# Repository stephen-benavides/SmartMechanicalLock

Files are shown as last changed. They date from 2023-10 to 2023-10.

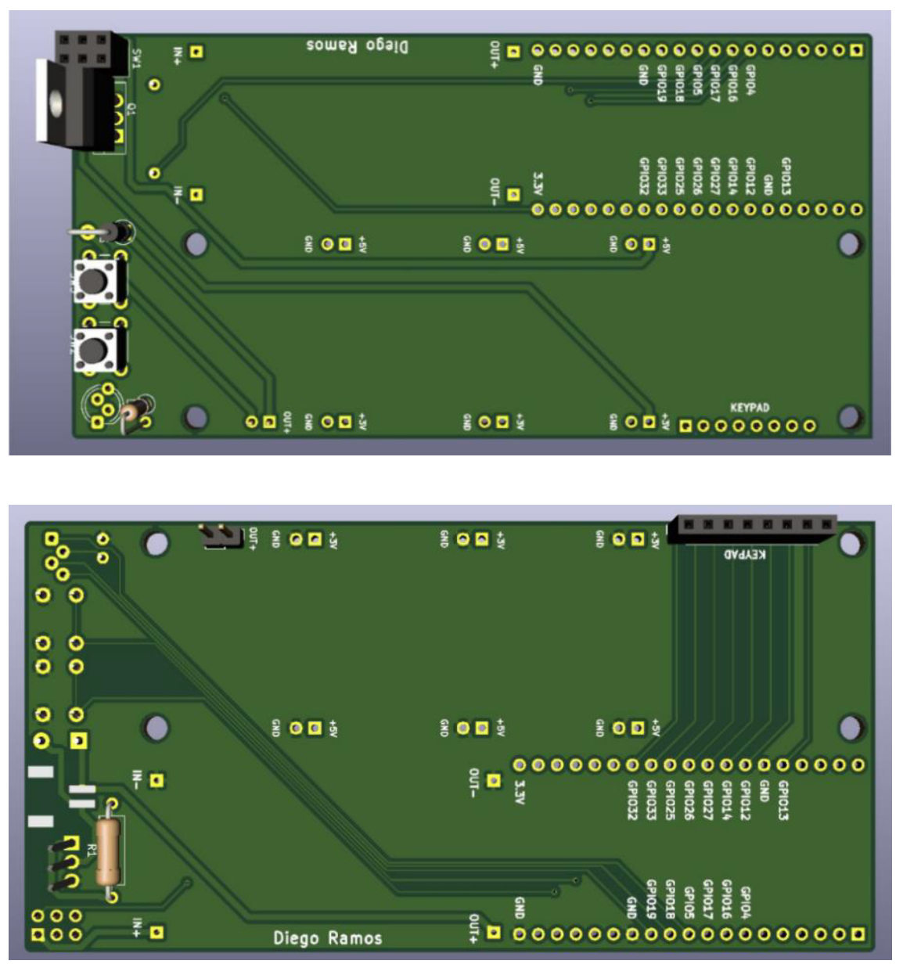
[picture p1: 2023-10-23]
Senior Project - Beta/Smart Lock (Pending Name)-20201122T195937Z-001/Smart Lock (Pending Name)/Schematics/Screen Shot 2019-09-06 at 3.24.47 PM.png

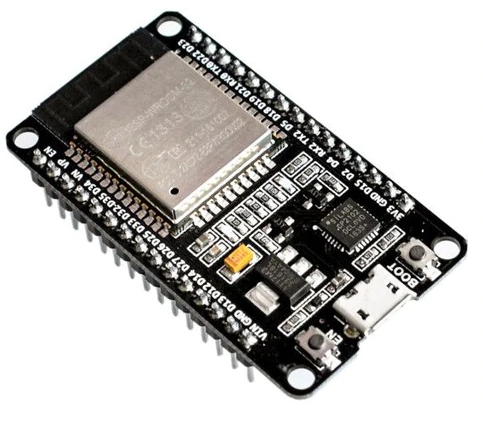
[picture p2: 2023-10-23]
Senior Project - Omega/ESP32/2019-02-23 (1).png

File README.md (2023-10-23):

# SmartMechanicalLock
Project contains all elements from the design of the PCB for the mechanical locks and its components as well as the mobile application to access the app to send the necessary commands to lock/unlock the lock and to store all sensible information within the cache of the android device

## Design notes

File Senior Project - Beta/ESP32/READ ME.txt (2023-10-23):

https://discordbots.org/servers/514901094950895651
wickr me 
null byte (Youtube)

arduino extension on visual studio code 
caprtea vacia, la abres con arduino uno . 

F1>Arduino initialize 

F1> carpeta en blanco (F1 hace todos los comandos)

F1> arduino examples
  > arduino config  
  > arduino serial monitor

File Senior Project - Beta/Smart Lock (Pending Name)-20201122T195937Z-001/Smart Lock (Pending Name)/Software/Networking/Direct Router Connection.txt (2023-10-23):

#include <WiFi.h>

void setup()
{
Serial.begin(9600);

  WiFi.disconnect();
  delay(3000);
  Serial.println("Initializing");
  WiFi.begin("wifi4beer","password");
  while ((!(WiFi.status() == WL_CONNECTED))){
    Serial.print("...");
    delay(300);

  }
  Serial.println("Connection Successful");
  Serial.println("Local IP address:");
  Serial.println((WiFi.localIP()));

}

void loop()
{

}

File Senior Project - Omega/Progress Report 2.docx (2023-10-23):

Project Work Progress Report No ______

Date:______________ Team #:_________

Project Title: _________________________________________________________

Submitted by: ___________________________________________________________

1. Project progress since last report:

Our goal this week is to be able to connect the ESP32 to a LAN network and stablish a control point for all the incoming connection using a cellphone as the router.

We were able to find the ESP32-WROOM-32D MCU IP address within the Arduino IDE serial monitor, now we are trying to send a pin signal to the computer wirelessly from the ESP32-WROOM-32D MCU.

2. Milestones achieved:
- Wireless connection stablished between the ESP32-WROOM-32D MCU and the computer by Stephen Benavides 02/20/2019
3. Problems and roadblocks, if any:
4. Is project on schedule? YES__X___ NO____
5. Next steps: (elaborate specifically on any problems listed in 3 and if the answer in 4. Is NO)

(You may use more pages, if needed)

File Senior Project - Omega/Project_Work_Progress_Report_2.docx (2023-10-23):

Project Work Progress Report No 2

Date: 02/23/2019 Team #: 33

Project Title: Anti-theft Package Security Home System (APSHS)

Submitted by Gregory Escobar, Stephen Benavides, Shawn Carnevale, Geomar Reyes

1. Project progress since last report:

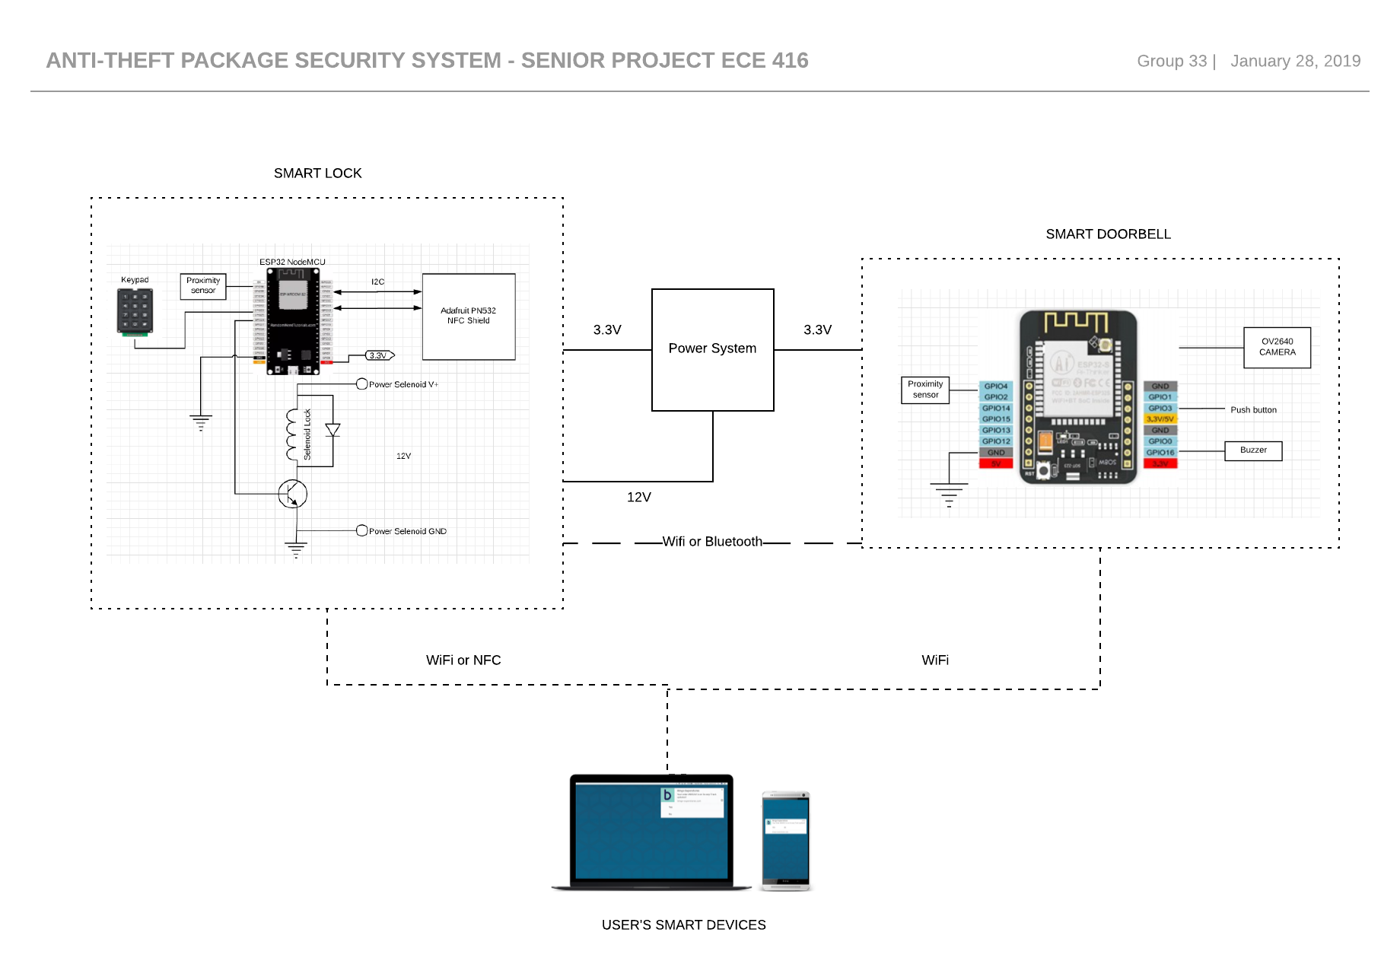
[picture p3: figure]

This is an updated version of the schematic for the whole project

Figure 1 Anti-theft package Security System

Communication between ESP32S and Adafruit PN532

Our team is still working to stablish communication between the ESP32-WROOM-32 and the PN532 using I2C communication protocol.

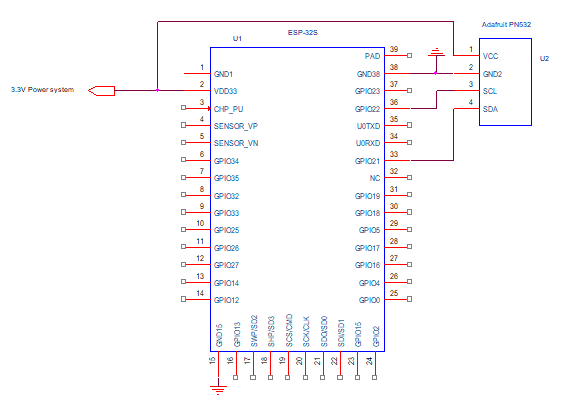
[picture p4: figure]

Figure 2 ESP32S and PN532 i2C wiring guide

Power System

For the power system our team have just picked out and received some new equipment. The focus this week was to find a way to charge and discharge the battery to and to keep a steady voltage because most of our components operate between 3.3-5 volts. The main issue was to design something that was simple and to keep it as affordable as possible. We found the solution of how to do that with a single component which was affordable and met our needs and specifications. Next week the goal will be to do more schematic work to finalize the design so we can move forward to start to build our power system onto a breadboard.

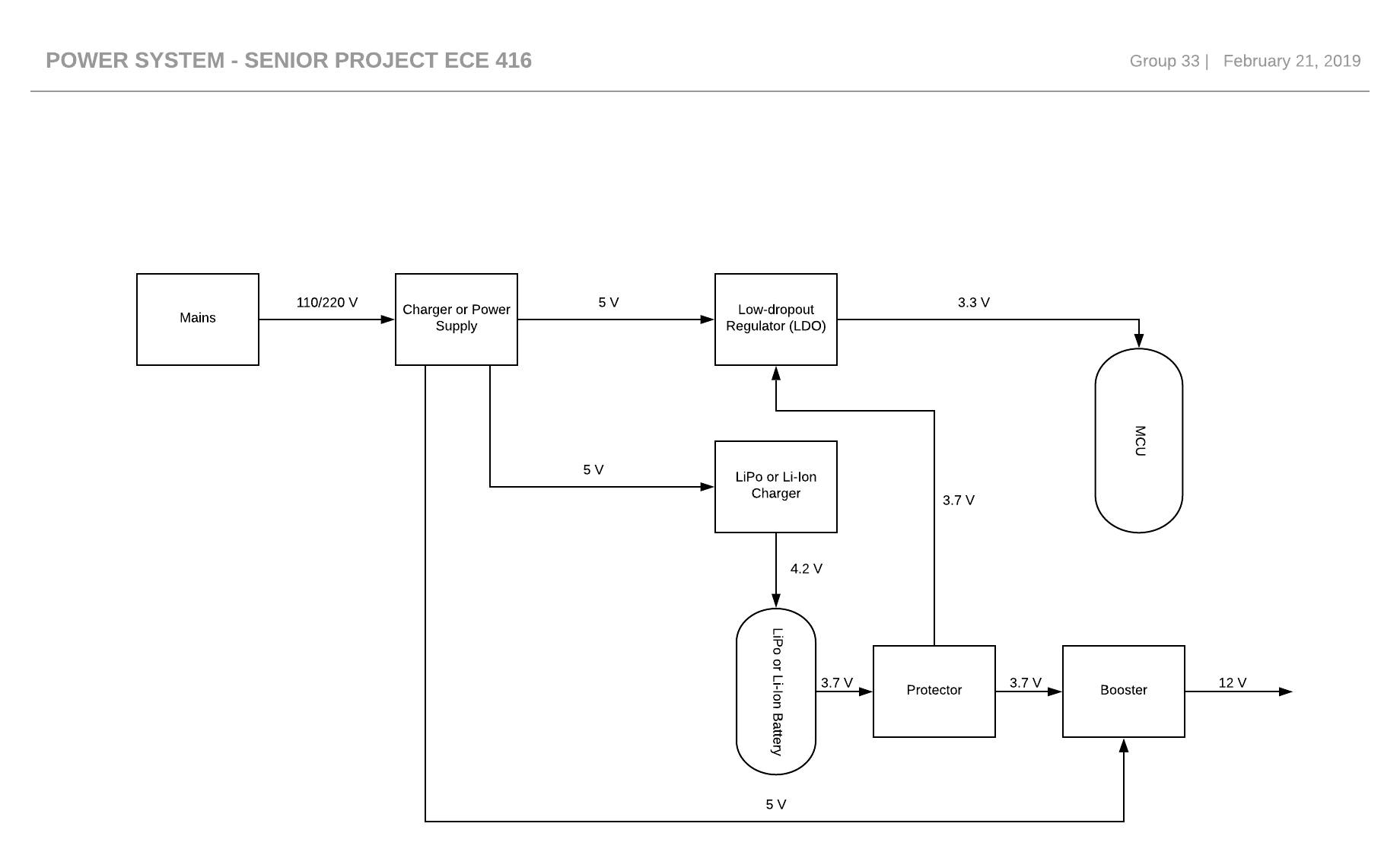
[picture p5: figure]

Figure 3 Power System

2. Milestones achieved:

Power System design was finalized by Shawn Carnevale and Gregory Escobar 02/21/19

3. Problems and roadblocks, if any:
4. Is project on schedule? YES__X___ NO____
5. Next steps: (elaborate specifically on any problems listed in 3 and if the answer in 4. Is NO) (You may use more pages, if needed)

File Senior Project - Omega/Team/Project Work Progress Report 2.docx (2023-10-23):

Project Work Progress Report No 2

Date: 02/23/2019 Team #: 33

Project Title: Anti-theft Package Security Home System (APSHS)

Submitted by Gregory Escobar, Stephen Benavides, Shawn Carnevale, Geomar Reyes

1. Project progress since last report:

Gregory Escobar and Shawn Carnevlale:

This is an updated version of the schematic for the whole project

Communication between ESP32S and Adafruit PN532

Our team is still working to stablish communication between the ESP32-WROOM-32 and the PN532 using I2C communication protocol.


Figure 1 Anti-theft package Security System


Figure 2 ESP32S and PN532 i2C wiring guide

Power System

For the power system our team have just picked out and received some new equipment. The focus this week was to find a way to charge and discharge the battery to and to keep a steady voltage because most of our components operate between 3.3-5 volts. The main issue was to design something that was simple and to keep it as affordable as possible. We found the solution of how to do that with a single component which was affordable and met our needs and specifications. Next week the goal will be to do more schematic work to finalize the design so we can move forward to start to build our power system onto a breadboard.


Figure 3 Power System

Stephen Benavides:

Our goal this week is to be able to connect the ESP32 to a LAN network and establish a control point for all the incoming connection using a cellphone as the router.

We were able to find the ESP32-WROOM-32D MCU IP address within the Arduino IDE serial monitor, now we are trying to send a pin signal to the computer wirelessly from the ESP32-WROOM-32D MCU.

I wanted to add Wireshark to our operations, but it might not be necessary yet. It is used for troubleshooting and diagnostic of the networks, this will be useful when trying the use the UART protocols to connect online using the web app to see if there are any problem with the connection.

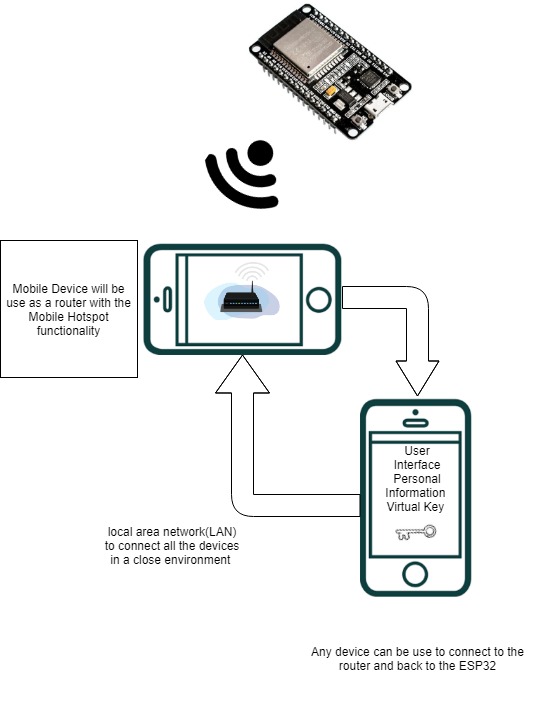
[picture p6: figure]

Figure 4. ESP32 connected to network

Geomar A. Reyes

Our goal for this week is to make the login page of the android app functional so that we can start to put name of customer and their ID in to a data base that will be connected to the app. This app will ask for a person username which will be provided by an administrator and the password will be made by the customer. The login screen will be able to match the username and password input by the customer with the one in the database.

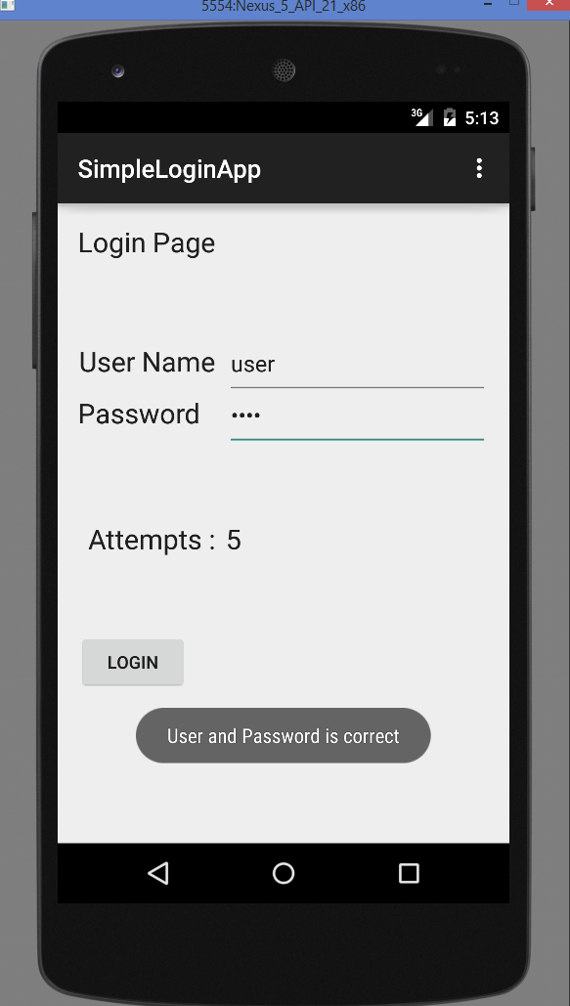
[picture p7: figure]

Figure 5. APP login screen

2. Milestones achieved:
- Power System design was finalized by Shawn Carnevale and Gregory Escobar 02/21/19
- Wireless connection stablished between the ESP32-WROOM-32D MCU and the computer finalized by Stephen Benavides. 02/21/19
- Finish the login screen of the android app and database system by Geomar Reyes 02/21/2019.
3. Problems and roadblocks, if any:
4. Is project on schedule? YES__X___ NO____
5. Next steps: (elaborate specifically on any problems listed in 3 and if the answer in 4. Is NO) (You may use more pages, if needed)

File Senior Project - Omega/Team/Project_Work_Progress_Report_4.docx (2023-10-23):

Project Work Progress Report No 4

Date: 03/31/2019 Team #: 33

Project Title: Intelligent Door System

Submitted by Gregory Escobar, Stephen Benavides, Shawn Carnevale, Geomar Reyes

1. Project progress since last report:

Hardware

The power system was tested in different scenarios. Results obtained showed that this system could power the microcontroller (ESP32), the solenoid and LEDs in case of a power outage for at least 10 hours due to the high capacity 18650 lithium cell. Solenoid was tested at different voltages in order to find the optimal input that would consume as low power as possible. GPIOs and power pins were finalized to proceed to PCB design.

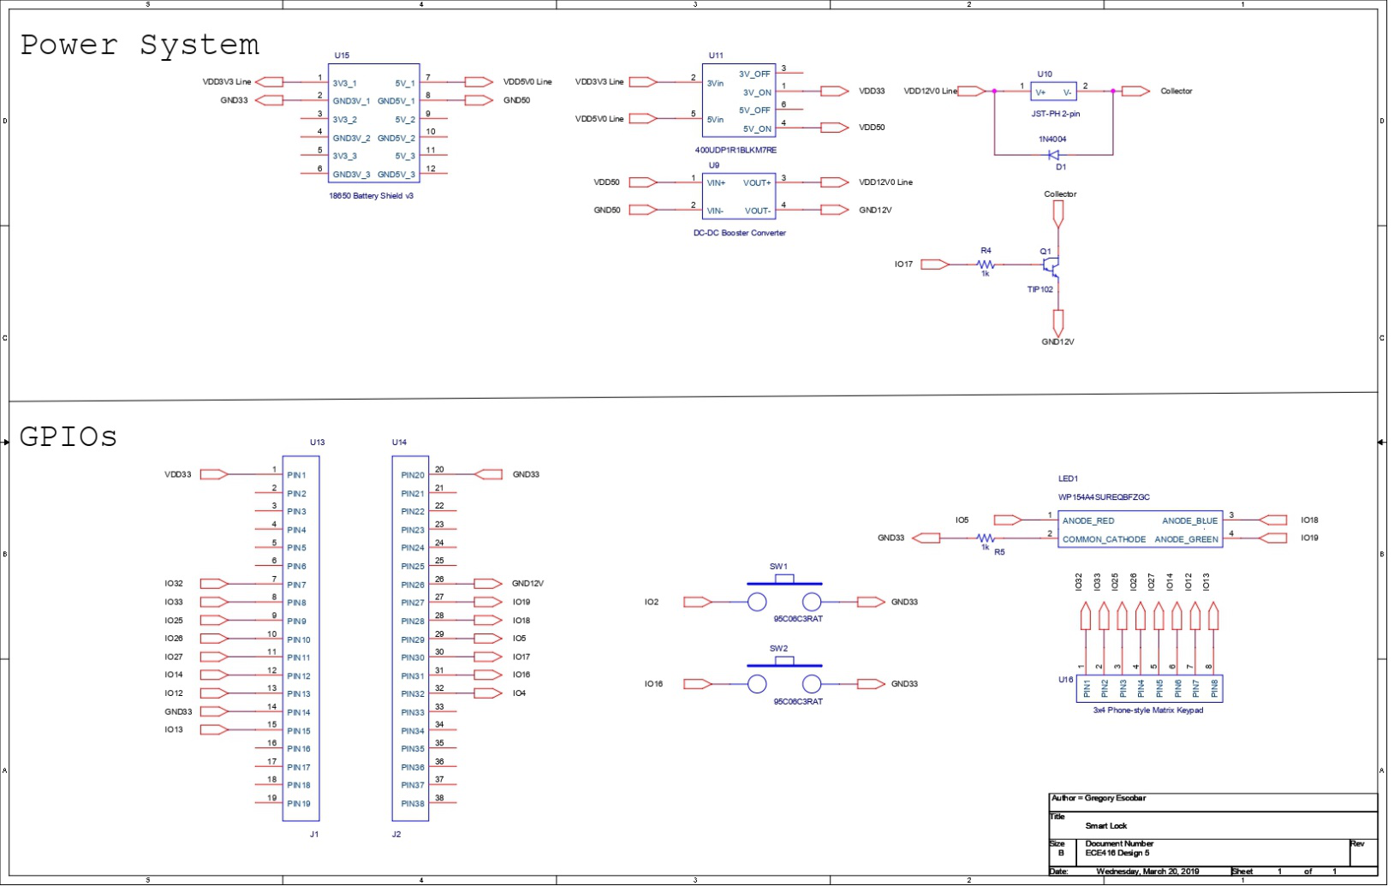
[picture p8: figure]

The PCB was custom designed with the help of Diego Ramos for convenience and precise connections. Components were selected and purchased on time.

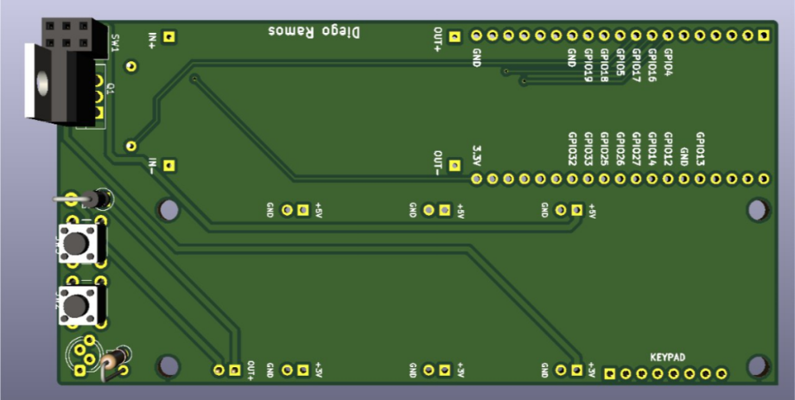
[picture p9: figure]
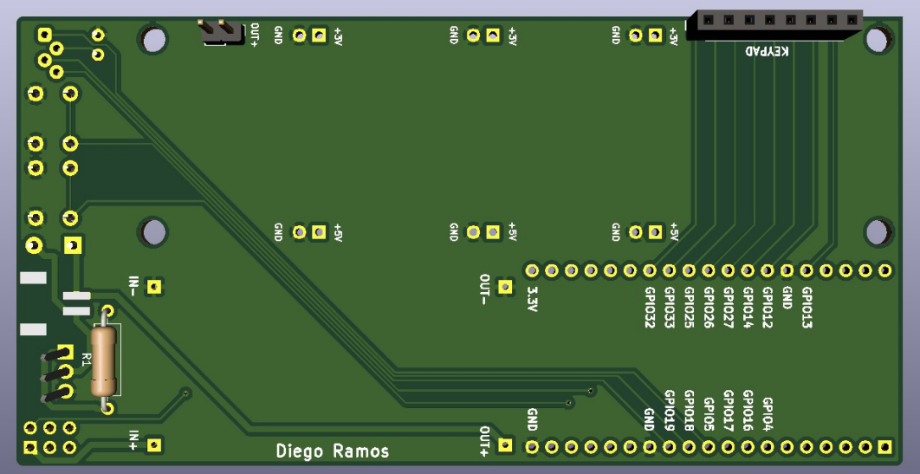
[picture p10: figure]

This is an updated block diagram of our project

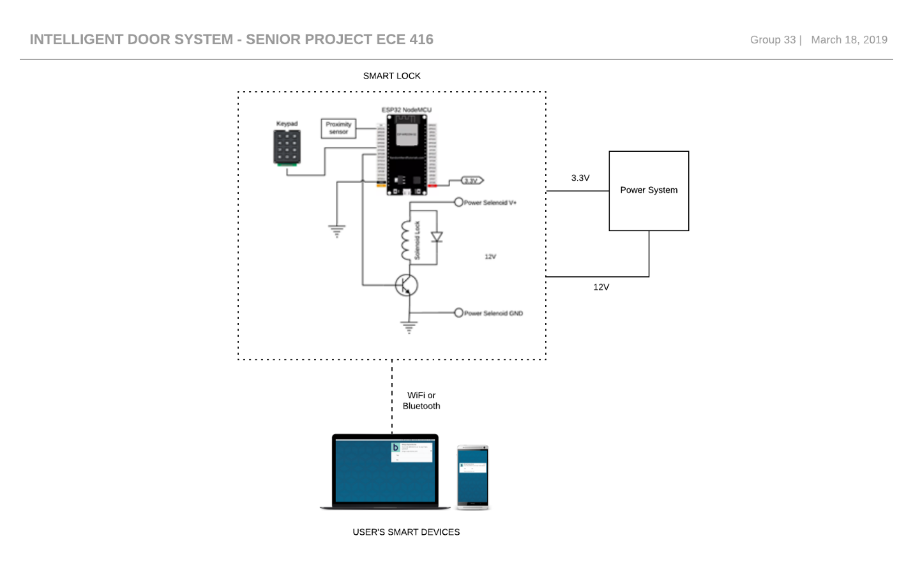
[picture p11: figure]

2. Milestones achieved:
- PCB design was finalized
- Components were solder and tested onto the PCB
- Keypad implementation initialized
3. Problems and roadblocks, if any:

Hardware

- Keypad Implantation
4. Is project on schedule? YES__X__ NO____
5. Next steps: (elaborate specifically on any problems listed in 3 and if the answer in 4. Is NO)

Keypad Implementation: The roadblocks we mainly encountered was with the keypad. Since the keypad was only Arduino compatible product, we had some issues with getting the keypad to work properly with the ESP32 and how to connect it to the ESP32. When we would press a 4 on the keypad the program would output a 6 and vice versa. After a further investigation as to why this was happening, we found out it had to do with the 4 and 6 being different resistances than the other keys. To fix this we had to modify our code and connect each key to different GPIOs to get the right results. After this, we are planning to add the keypad to our security system by allowing the user to select a 4 digit passcode.

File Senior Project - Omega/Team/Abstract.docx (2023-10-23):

Wireless Lock System

Abstract

Team members: Stephen Benavides, Shawn Carnevale, Gregory Escobar, and Geomar Reyes.

Advisors: Dr. Leonid Tsybeskov , Dr. Marek Sosnowski, and Professor Mohammed Feknous

Our project consists of designing a user-friendly security door system. The idea behind our project is to create a system that uses an electronic door lock with wireless communication module so that a person in the possession mobile device can get access to a secured area. Our project will be designed to provide security to the customer that will buy our product. This security is going to be in the form of an encrypted communication system that will make sure that you are authorized to be in a specific area. A mobile phone application or computer software will be used to display any important information and configure the system

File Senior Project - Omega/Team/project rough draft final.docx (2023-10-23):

Intelligent Door System

Group #33 3333 33

Team Members:

Gregory Escobar

Stephen Benavides

Shawn Carnevale

Geomar A. Reyes

Advisor:

Dr. Sosnowski

Area of Study:

Computer Engineering

Electrical Engineering

Submission date:

4/7/2019

Abstract:

The name of this project is intelligent door system. Our team members are Gregory Escobar, Stephen Benavides, Shawn Carnevale and Geomar A. Reyes. The name of our advisor is Marek Sosnowski. The ideal behind our project is to create an intelligent door lock that can be lock and unlock through a cellphone app. Also this intelligent door lock has to be able to unlock and lock the door lock through a keypad just in case a person loses the phone.

Table of content:

Abstract …………………………………………………….2

1. Introduction…………………………………………..4
2. Project accomplishment ……………………………..5
3. Budget ………………………………………………...10
4. Acknowledgment……………………………………..11
5. Reference……………………………………………...11
6. Appendices……………………………………………..12
1. Introduction

The ongoing evolution of the network of computing devices embedded in everyday objects to transmit and receive data better known as the Internet of Things (IoT) has enabled devices to become smart objects. For our senior project we wanted to do something that could be practical, have multiple uses, and would be marketable to the public. Everyone likes the feeling of their house being secure. For this reason, we decided to do a security system. Our previous proposal we were interested in designing an Intelligent Door System. Unfortunately, due to time constraints and our project getting more complex the scope of the project changed from being marketed to the industry and residential homes to being strictly marketed to residential homes.

When we were in the design phase of the project we were influenced by the Ring Door Bell and the Nest Padlock. What we liked about the Ring Door Bell is the built-in camera. When someone comes into the vicinity of the doorbell the camera turns on and your phone will get a notification and you can see through your phone who is at your door step. This concept alone made us interested implementing a camera because previously we only had our project lock and unlock a door so we wanted to make our project more interesting. Another item that influenced our project is the Nest Padlock. How this worked is you download an application on your phone. Once downloaded you can lock or unlock your door through your phone. It also has a keypad on it so instead of giving someone a key you can give them a passcode. What aspects of the Nest Padlock influenced our project is the application on your phone, being able to lock or unlock your door through your phone, and that the user doesn’t need a key. This also replaces deadbolt doors and someone would not have to deal with losing keys.

Our original intention for our project was we wanted the user to able to lock and unlock the door. If somebody entered the wrong passcode the user would get a notification on their phone and the camera would turn on and the user could see who was at the door. Unfortunately, due to time constraints and shipping issues we were not able to add the camera module to our project. Since it would be too expensive and complex to implement it onto a door we instead have 3D printed enclosure with a moveable part. What will happen is when the user wants to unlock the door the user will open an application on their phone and enter a username and password. When the user enters the correct information, the application will go to a new page and the user can tap an open icon on their phone. Once the user presses the open icon a solenoidal lock will get energized and the movable part will be unlocked. At this point the user has the option to lock the door by pressing the close icon on the phone application or the solenoid will get un-energized in thirty seconds. In the case of a power outage there is a keypad where if you enter the correct passcode you unlock the door. If somebody enters the wrong passcode you will get a notification on your phone telling you somebody entered the wrong passcode.

Project Objectives

For our project our objective was to design a residential security system. When considering how we would design it we put took some stuff into consideration. The first consideration was to make it affordable because of limited funds. Another thing we took into consideration is making it simple enough to build. Since we have a time constraint we wanted to make sure we were able to complete our project and make it as interesting as possible.

Project Significance

What makes our project significant is the application of the security of homes. Everybody likes to feel safe when they are in their home and want to make sure that when they are not home their home is secure. This reason alone makes our project significant. Parks Associates in 2018 estimate that by 2021 27% of Americans will have security systems installed in their homes proving that more people in the America are getting interested in equipment that helps make their home more secure. It allows the user to integrate the regular key that is usually used to a smartphone and make it more practical.

Project Novelty

When looking at what the market has to offer for residential security systems we noticed we have aspects that make our project unique. The main reasons why our project is different is than what is offered on the market is our software.

2. Project accomplishments

2.1 Technical details

Hardware

Power and Battery: It consists of the following three components

- 100 - 240V 50/60Hz AC Adapter (5V 1A).
- Panasonic NCR18650B lithium battery 3.7V
- Wemos 18650 Battery Shield v3

The power system was designed to behave as an uninterruptable power supply by allowing the user to power the electronic using an AC-DC convert adapter (5V 1A) and in case of a power outage condition it will be powered by a high capacity lithium battery. It provides the system with a 3.3V line for the microcontroller and12V line for the solenoid. The battery shield consists of a 1A Standalone Linear Li-Ion Battery Charger with Thermal Regulation (TP4056), three low voltage dropout CMOS voltage regulators (LDO 3.3V) and a LM2577 step up voltage regulator (3.3V to 8V). A block has been attached to the appendix of this paper.

Microcontroller:

- ESP32S Node MCU

The ESP32S is a single chip microcontroller with 2.4 GHz Wi-Fi-and-Bluetooth capabilities that targets a wide variety of applications that required low power consumption and good RF performance. It uses two adjustable clock frequency (80-240MHz) 32-bit Xtensa LX6 processors that use the Tensilica ISA. ESP32S integrates a rich set of peripherals, ranging from capacitive touch sensors, Hall sensors, low noise sense amplifiers, SD card interface, Ethernet, high speed SDIO/SPI, UART, I2S and I2C. This microcontroller supports data rates up 150Mbps and 20dBm output power at the antenna. The ESP32S was designed using the TSMC ultra-low-power 40 nm technology.

Lock-Style Solenoid:

- 12VDC (you can use 9-12 DC volts, but lower voltage results in weaker/slower operation)
- Draws 650mA at 12V, 500 mA at 9V when activated
- Designed for 1-10 seconds long activation time
- Max Dimensions: 41.85mm / 1.64" x 53.57mm / 2.1" x 27.59mm / 1.08"
- Dimensions: 23.57mm / 0.92" x 67.47mm / 2.65" x 27.59mm / 1.08"
- Wire length: 222.25mm / 8.75"
- Weight: 147.71g

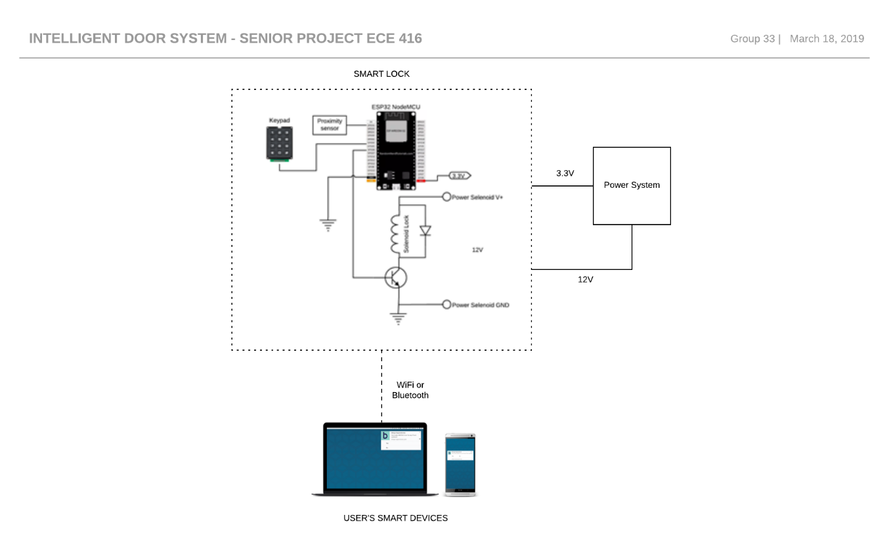
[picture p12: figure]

Engineering Standards:

FCC title 47 CRF part 15: The smart lock complies with the FCC title 47 CRF part 15 regulates everything from spurious emissions (https://en.wikipedia.org/wiki/Spurious_emission) to unlicensed low-power broadcasting (https://en.wikipedia.org/wiki/Low-power_broadcasting).

IEEE 802.11b Standard: It has a maximum raw data rate of 11 Mbit/s, and uses the same media access method defined in the original standard. 802.11b products appeared on the market in early 2000, since 802.11b is a direct extension of the modulation technique defined in the original standard.

IEEE 802.11g Standard: This works in the 2.4 GHz band (like 802.11b), but uses the same OFDM (https://en.wikipedia.org/wiki/Orthogonal_frequency-division_multiplexing) based transmission scheme as 802.11a. It operates at a maximum physical layer bit rate of 54 Mbit/s exclusive of forward error correction codes, or about 22 Mbit/s average throughput.

IEEE 802.11n Standard: It is an amendment that improves upon the previous 802.11 standards by adding multiple-input multiple-output (https://en.wikipedia.org/wiki/Multiple-input_multiple-output) antennas (MIMO). 802.11n operates on both the 2.4 GHz and the 5 GHz bands.

IEEE 802.15.1 WPAN/Bluetooth Standard: It defines physical layer (PHY) and Media Access Control (https://en.wikipedia.org/wiki/Media_Access_Control) (MAC) specification for wireless connectivity with fixed, portable and moving devices within or entering personal operating space.

2.2 Testing and Performance Measures

The system was tested to estimate operation time and the power consumption in case of a power outage condition. The ESP32S Node MCU + electronics (LEDs and keypad) was estimated to consume 38mA when the CPU is operating at 80MHz clock frequency. Since this microcontroller operates at 3.3V the power consumption is about ~125.4mW. The solenoid consumes 400mA at 9V meaning that the power consumption is about ~3.6W. The time that the solenoid consumes such power is limited by the software implementation. The capacity of the battery that is used on the system is 3500mAh. Therefore, the lock can operate for at least 8 hours in case of a power outage.

2.3 Future Potential

The project could be enhanced by implementing different method of authentication like biometric or face recognition.

2.4 Learning Experience

The project allowed us to learn about PCB design, soldering skills, power electronics and network design.

Software:

The ESP 32 software has been successfully implemented into the hardware. The team was able to test the Wi-Fi connection by using a cellphone with hotspot included as a router to transmit a signal between the ESP32 and the APP by using the mobile network provided by AT&T. The test was successful, so we were able to send the right signal from the APP to the lock to open or close it at will. Our next goal was to check if the app was able to communicate across networks that are intended to be used by outside guests such as the ones that you get at a coffee shop, they are usually open for everyone and unsafe. For this test, we used NJITguest with a student credential to access. Unfortunately, the NJIT network asks for a specific set of permissions and confirmations when accessing their network; therefore, the test for direct connection with the NJIT network was unsuccessful. Then we decided to use a “router” to redirect the signal from the NJIT into the ESP 32. We were able to do so by sharing hotspot with the cellphone to the esp32, but instead of using the mobile connection we shared the NJIT Wi-Fi through the phone. Thus, proving that we can connect our device on any network that has a router to redirect the signal.

Application

• Our goal was to add a background for the app, we made it look more professional and user friendly • We tested the communication between the hardware and the app through the ESP 32 • A link was successfully created between the app and the ESP32 • The user interface can store the username and password by using a TinyDB to store that information in the app’s cache • The user interface sends error messages when the username or password is incorrect

Network Framework

• Connection has been made successfully between the lock, the esp32 and the application. • The ESP 32 can now build a web server to send and receive requests from the exterior. • A protocol has been implemented into the esp32 to change the way in which we access into the server. We no longer have to put an IP address into the search bar of any device connected in LAN, now we can use an specific name to make it easier to access i.e. from http://192.168.43.57 we changed it to http://smartlock.local • The code that requests signals from the ESP 32 has been modified using an encrypted password, and the only way to decrypted is by using the app.

Future Upgrades

• Implement a method to send messages to the user when initializing the smart lock for the first time • Implement a method to send messages to the user every time the door has been access • The messages will be sent to the costumer via text messages and email to make it safer. The user will have control over everything that happens around the lock on real time

• Create a dedicated web server http://smartlock.local where the user is going to be able to know the status of the lock. i.e. How long the door has been active for as well as the temperature of the internal mechanisms.

3. Budget

Name | Quantity | Price
12V Electronics Lock Assembly Solenoid Low Power Consumption | 1 | $17.61
ESP32S | 1 | $11
1N4004 Diode | 1 | $0.05
TIP102 Transistor | 1 | $1.60
Wemos 18650 Battery Shield v3 | 1 | $3.0
DC-DC boost converter | 1 | $8.00
Single Pole Double Throw Switch | 1 | $1.62
RGB LED WP154A4SUREQBFZGC | 1 | $1.88
Pushbutton | 2 | $0.42
Female Headers | 2 | $2.00
| Total | $47

4. Acknowledgements

We thank Diego Ramos, EE student, for helping us designing the PCB for the project.

5. References

“IEEE 802.11.” Wikipedia, Wikimedia Foundation, 6 Apr. 2019, en.wikipedia.org/wiki/IEEE_802.11#802.11b.

“IEEE 802.15.” Wikipedia, Wikimedia Foundation, 26 Mar. 2019, en.wikipedia.org/wiki/IEEE_802.15#Task_group_1_(WPAN/Bluetooth).

Pluvinage, Lucas. “The Xtensa Architecture.” MirageOS on ESP32 - a Tale of Cross-Compilation, 28 Mar. 2018, www.lortex.org/posts/esp32/2018/03/28/the-xtensa-architecture.html.

ESP32 Overview | Espressif Systems, www.espressif.com/en/products/hardware/esp32/overview.

Appendices

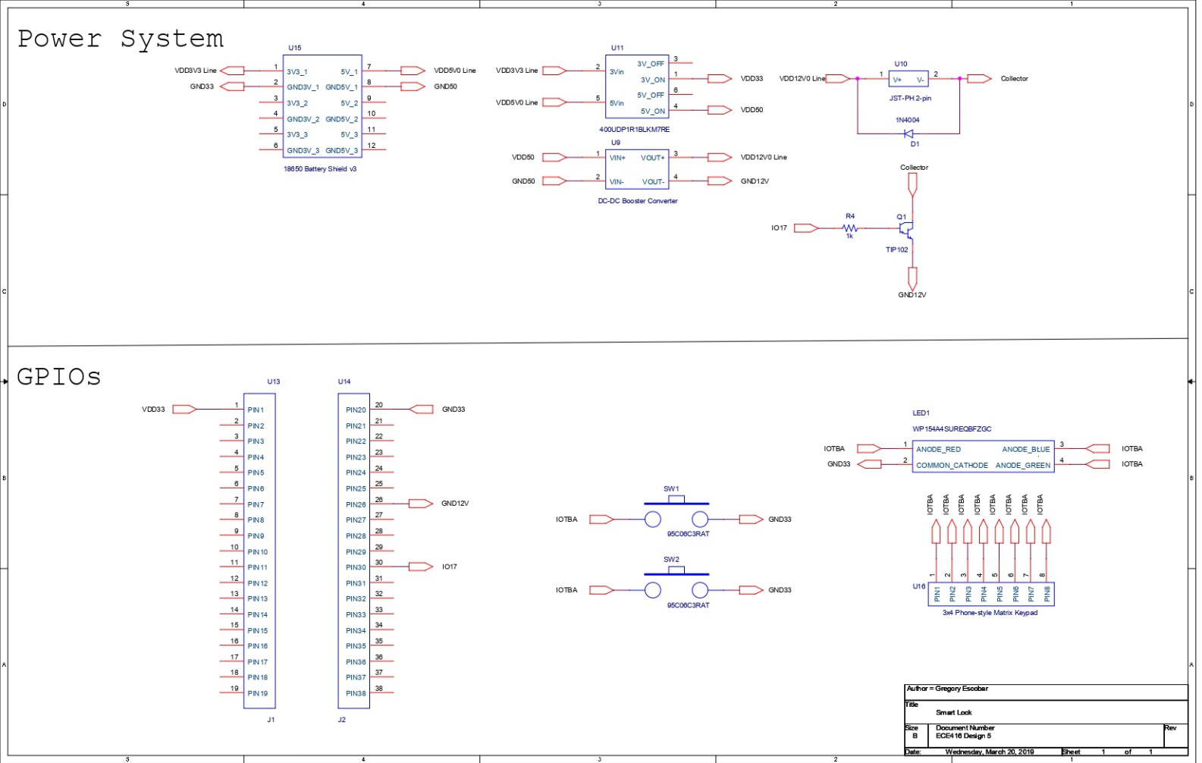
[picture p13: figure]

Figure 1 Smart Lock Schematic

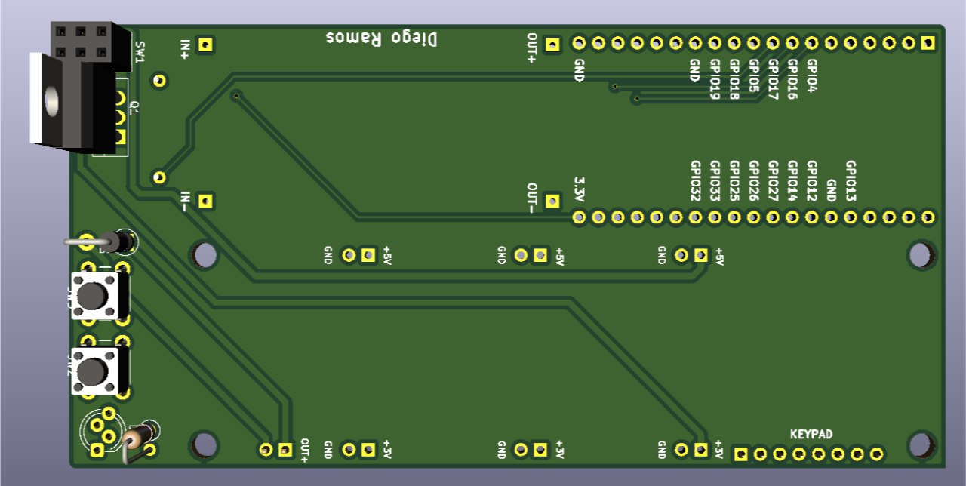
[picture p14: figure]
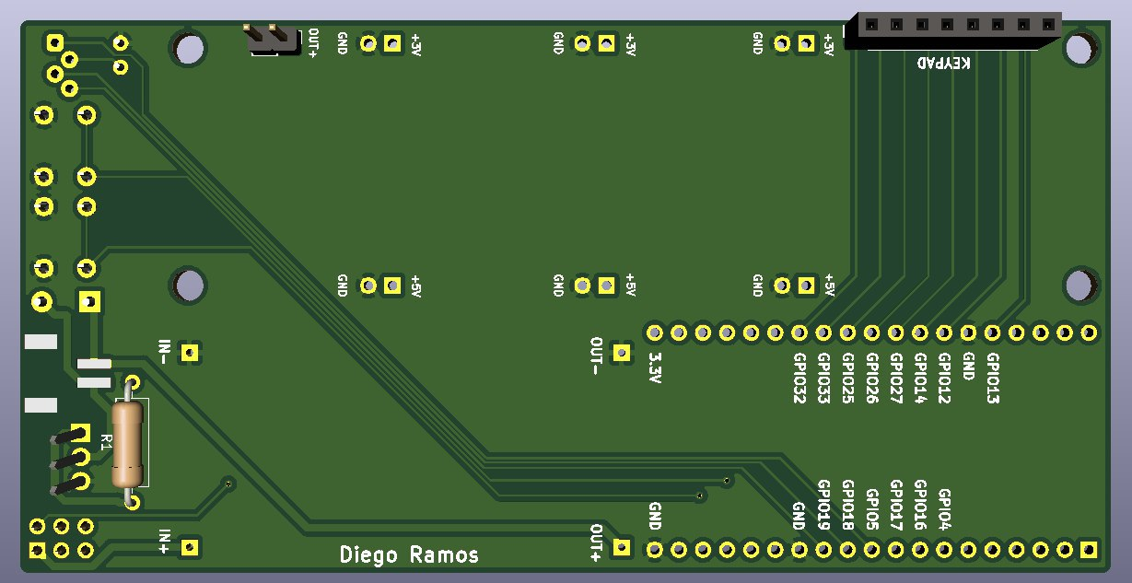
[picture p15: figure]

App code:

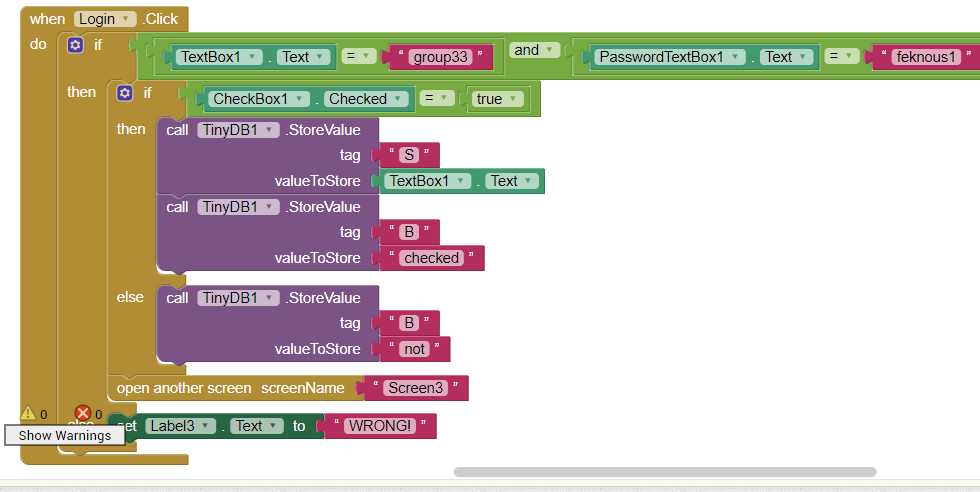
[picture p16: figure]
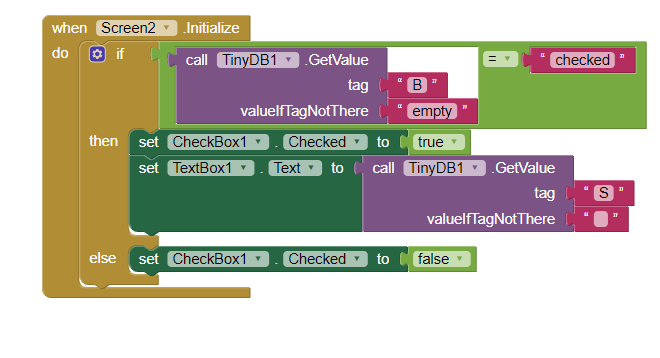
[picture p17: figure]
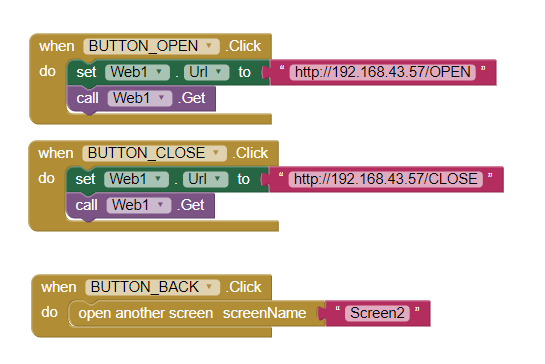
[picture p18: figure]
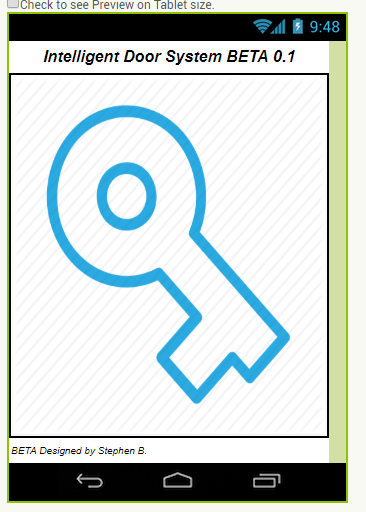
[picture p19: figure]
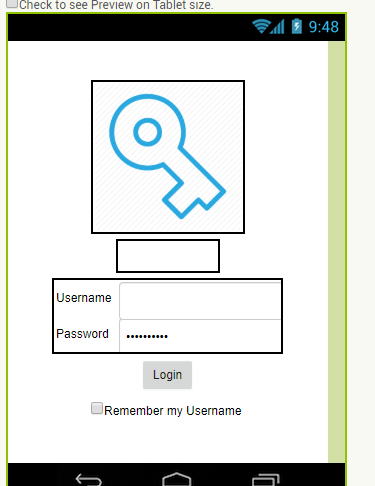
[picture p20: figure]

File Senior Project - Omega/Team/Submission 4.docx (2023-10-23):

Project Work Progress Report No 4

Date: 03/31/2019 Team #: 33

Project Title: Anti-theft Package Security Home System (APSHS)

Submitted by Gregory Escobar, Stephen Benavides, Shawn Carnevale, Geomar Reyes

1. Project progress since last report:

Hardware


The power system was tested in different scenarios. Results obtained showed that this system could power the microcontroller (ESP32), the solenoid and LEDs in case of a power outage for at least 10 hours due to the high capacity 18650 lithium cell. Solenoid was tested at different voltages in order to find the optimal input that would consume as low power as possible. GPIOs and power pins were finalized to proceed to PCB design.

The PCB was custom designed with the help of Diego Ramos for convenience and precise connections. Components were selected and purchased on time.

This is an updated block diagram of our project

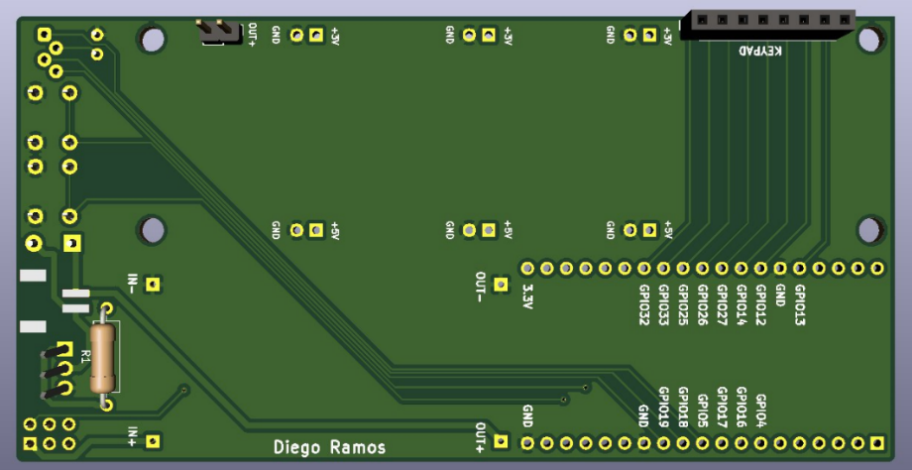
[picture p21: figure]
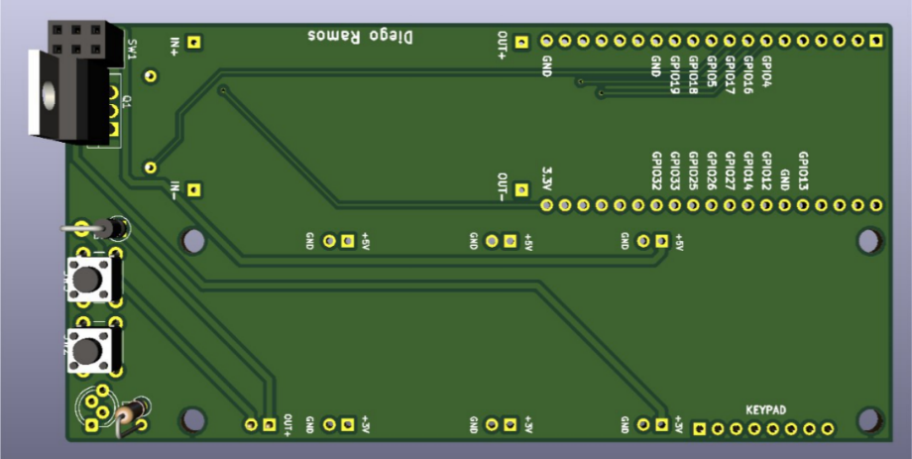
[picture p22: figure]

Software:

The ESP 32 software has been successfully implemented into the hardware. The team was able to test the Wi-Fi connection by using a cellphone with hotspot included as a router to transmit a signal between the ESP32 and the APP by using the mobile network provided by AT&T. The test was successful, so we were able to send the right signal from the APP to the lock to open or close it at will. Our next goal was to check if the app was able to communicate across networks that are intended to be used by outside guests such as the ones that you get at a coffee shop, they are usually open for everyone and unsafe. For this test, we used NJITguest with a student credential to access. Unfortunately, the NJIT network asks for a specific set of permissions and confirmations when accessing their network; therefore, the test for direct connection with the NJIT network was unsuccessful. Then we decided to use a “router” to redirect the signal from the NJIT into the ESP 32. We were able to do so by sharing hotspot with the cellphone to the esp32, but instead of using the mobile connection we shared the NJIT Wi-Fi through the phone. Thus, proving that we can connect our device on any network that has a router to redirect the signal.

Application

- Our goal was to add a background for the app, we made it look more professional and user friendly
- We tested the communication between the hardware and the app through the ESP 32
- A link was successfully created between the app and the ESP32
- The user interface can store the username and password by using a TinyDB to store that information in the app’s cache
- The user interface sends error messages when the username or password is incorrect

Network Framework

- Connection has been made successfully between the lock, the esp32 and the application.
- The ESP 32 can now build a web server to send and receive requests from the exterior.
- A protocol has been implemented into the esp32 to change the way in which we access into the server. We no longer have to put an IP address into the search bar of any device connected in LAN, now we can use an specific name to make it easier to access i.e. from http://192.168.43.57 we changed it to http://smartlock.local
- The code that requests signals from the ESP 32 has been modified using an encrypted password, and the only way to decrypted is by using the app.

Future Upgrades

- Implement a method to send messages to the user when initializing the smart lock for the first time
- Implement a method to send messages to the user every time the door has been access
- The messages will be sent to the costumer via text messages and email to make it safer. The user will have control over everything that happens around the lock on real time
- Create a dedicated web server http://smartlock.local where the user is going to be able to know the status of the lock. i.e. How long the door has been active for as well as the temperature of the internal mechanisms.
1. Milestones achieved:
- PCB design was finalized
- Components were solder and tested onto the PCB
- Keypad implementation initialized
- Connection between the app, ESP 32 and lock was finalized
- Encrypted passwords have been implemented
- Encrypted requests from the server has been implemented
- The ESP32 only responds to the users with the app
- The app has become the solely virtual key for the lock
2. Is project on schedule? YES__X__ NO____
3. Next steps: (elaborate specifically on any problems listed in 3 and if the answer in 4. Is NO)

Keypad Implementation: The roadblocks we mainly encountered was with the keypad. Since the keypad was only Arduino compatible product, we had some issues with getting the keypad to work properly with the ESP32 and how to connect it to the ESP32. When we would press a 4 on the keypad the program would output a 6 and vice versa. After a further investigation as to why this was happening, we found out it had to do with the 4 and 6 being different resistances than the other keys. To fix this we had to modify our code and connect each key to different GPIOs to get the right results. After this, we are planning to add the keypad to our security system by allowing the user to select a 4-digit passcode.

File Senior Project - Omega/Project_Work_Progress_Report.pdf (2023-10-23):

Project Work Progress Report No 2

Date: 02/10/2019 | Team #: 33
Project Title: Anti-theft Package Security Home System (APSHS)
Submitted by: Gregory Escobar, Stephen Benavides, Shawn Carnevale, Geomar Reyes

### 1. Project progress since last report:

We are currently working with the ESP32-WROOM-32D MCU and the PN532 NFC shield. We are learning how to program them since the ESP32-WROOM-32D arrived on 02/07/2019. We are using these two components to implement the Smart Lock module. This week we are going to keep testing communication between these two components as well as the implementation of a simple LAN network.

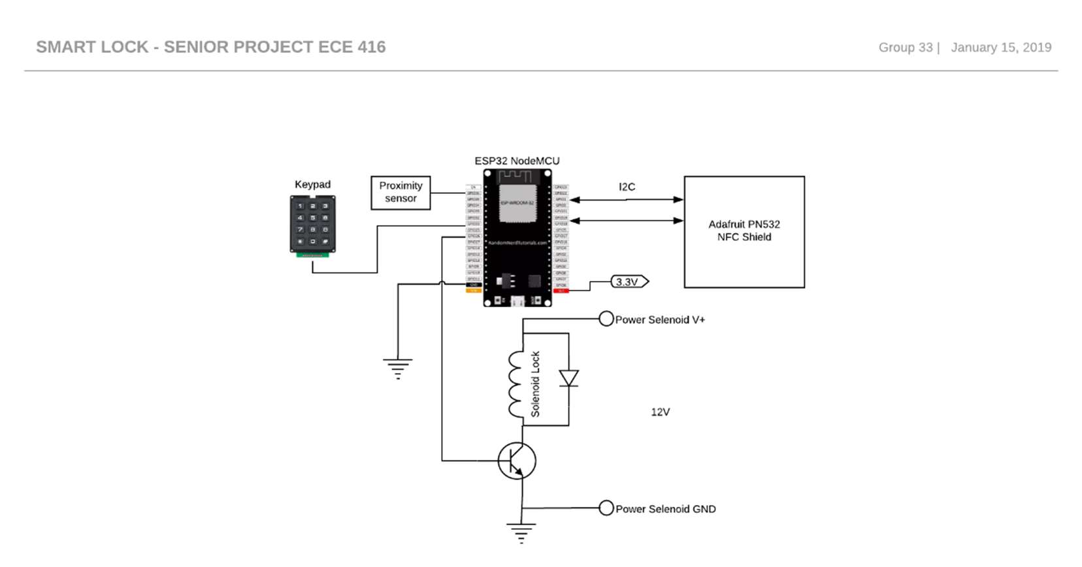
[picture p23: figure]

Schematic and with the specific pins to accomplish the communication between modules have been finalized.

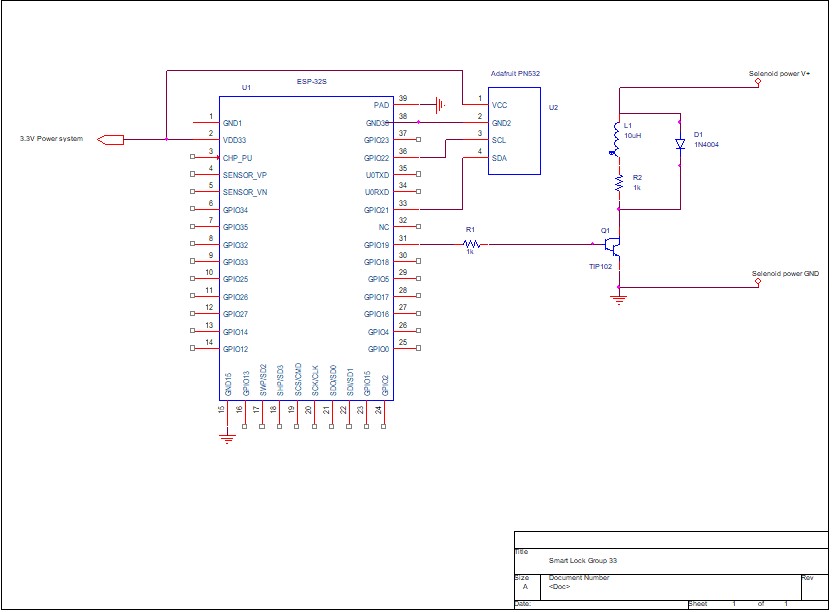
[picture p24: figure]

We are also still designing the extra module added to the project so the project will become more interesting. This module is the Smart Doorbell. Research is being done on how to implement the face recognition algorithm. A proximity sensor has to be implemented to enhance low power consumption by decreasing the time the camera will be on.

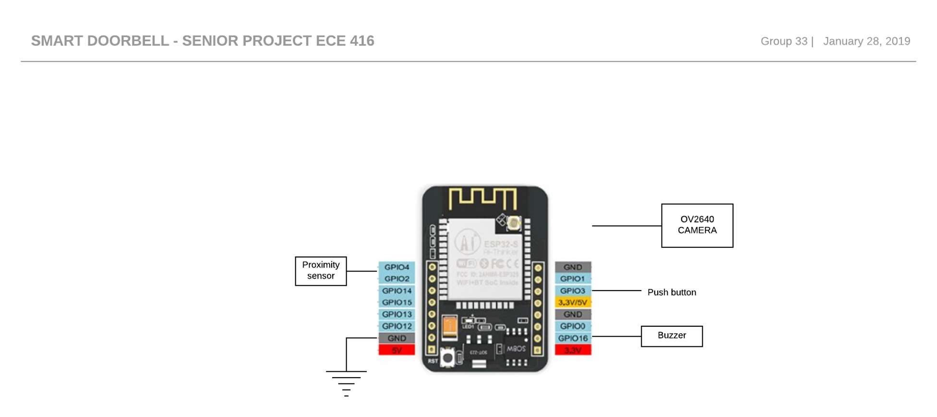
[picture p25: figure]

Emergency power system has not been designed yet but the hardware group will be designing it during this week.

### 2. Milestones achieved:

- Stablished communication between Adafruit PN532 and ESP32-WROOM-32D using I2C communication protocol 02/10/2019 – Gregory Escobar
- Login screen finalized using Android Studio App 02/08/219 – Geomar Reyes
- ESP32-WROOM-32D was successfully added to a Local Area network (LAN) 02/10/2019 – Stephen Benavides.
- Power supply AC-DC 3.3V power system for Smart Lock module design finalized 02/10/2019 – Shawn Carnevale.

### 3. Problems and roadblocks, if any:

Face recognition algorithms are very complex. Implementation and designing can be a time-consuming process.
ESP32-CAM MCU used to implement the Smart Doorbell Module got backorder which decreases the time to test face recognition.
4. Is project on schedule? | YES__X___ | NO____

5. Next steps: (elaborate specifically on any problems listed in 3 and if the answer in 4. Is NO) (You may use more pages, if needed)
Even though face recognition is a very complex algorithm to implement, there are many resources online that can help us achieve the purpose of our project. There are many libraries on Python that make the implementation of Face recognition much easier. There are many people that have also implemented face recognition with the same module we have ordered and succeed on the process. We are working using these resources and the code can be tested on the MCU we currently have because it is similar to the module that got backordered.

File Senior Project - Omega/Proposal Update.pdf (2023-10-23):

ECE 416- Updated Project Description and Schedule

Date: 02/05/2019 | Team #: 33

Project Title last semester: Smart Door Intelligent system
Project Tittle this semester: Anti-theft Package Security Home System (APSHS)

Team members: Gregory Escobar, Stephen Benavides, Shawn Carnevale, Geomar Reyes

### 1. Describe changes in the project if different form the proposal

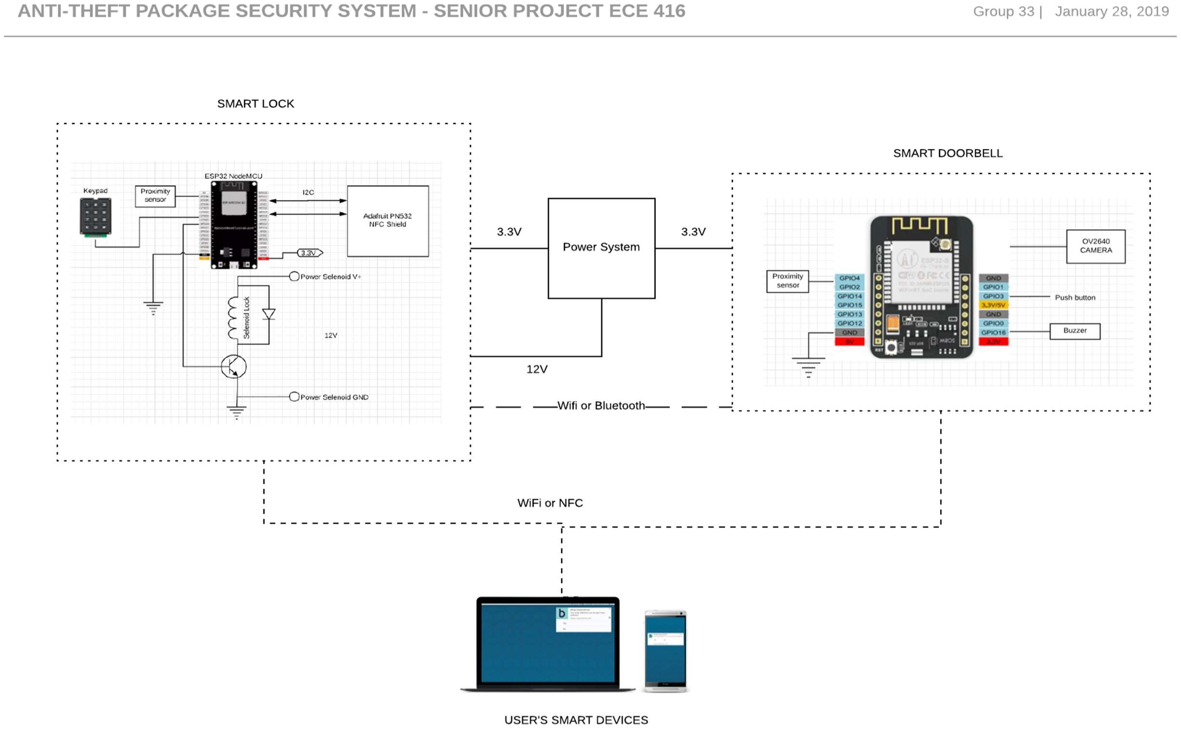
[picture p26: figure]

Figure 1 Block Diagram Group 33

For our project we have added some components to make it more interesting. The major change we made was adding the Smart Doorbell module to the project. The Smart Doorbell consists of a Wi-Fi camera module that will use face recognition to alert the user when someone is at the door trying to pick a delivered package. There will be two proximity sensors to detect when someone is at the door. One proximity sensor will be on the Smart Lock module and the other one on the Smart Doorbell module. The camera module will turn on when someone is in range of both the sensors. Once the camera senses who is there will be a signal sent to the person to notify that someone is at the door. There will be a list of parameters to indicate if someone should or shouldn't be at the door. If someone isn't supposed to be at the door a notification will be sent to the user and a buzzer will go off. The Smart Doorbell circuit though is tentative, and we are not sure if this is the final product. We are also currently working on a emergency power system for our project in the event that a power outage were to occur.

### 2. Work performed and milestone achieved since the approval of the proposal in ECE 414

We removed the Arduino MCU due to its lack of Wi-Fi interface 01/15/19

We ordered main components for Smart Lock module 01/16/19

We selected ESP32 as our main MCU 01/20/19

We decided to remove the linear actuator 01/22/19

Designed preliminary schematic for Smart Doorbell Module that will use face recognition 01/28/19

Android App login screen was developed on 01/29/2019

We decided to add the DC-DC converter to step up the voltage because of the amp draw of the solenoid lock 02/01/19

### 3. List major parts and components (microcontollers, sensors, actuators). Indicate if

delivered or still need to be obtained.

Name | Description | Quantity | Price | Link | Distributor | Status | Datasheet
| | | | | | | Link 1
1

Adafruit PN532 NFC/RFID
Controller Shield for Arduino

Shield for the arduino to

enable NFC | 1 | $39.95 Link 1 | Amazon/Adafruit | Received on 01/19

Link 2

2

Robodo Electronics
SLNDLTCH12 12V Electronics
Lock Assembly Solenoid Low
Power Consumption | Electric lock for the door

1
| | $17.61 | Link 1 | Amazon/Adafruit | Received on
| | | | | 01/19 | Link 1

### 3 ESP32

Microcontroller with WiFi

capabilities like the ESP8266 | 1 | $11 | Link 1 | Amazon/Hitlego | Received on
| | | | | 01/31/19 | Link 1

### 4 ESP32 - CAM

WiFi module for Smart
Doorbell | 1 | $7.50 | Link 1 | Banggood/Geekcreit | In Transit | Link 1

5 1N4004 Diode

Protection diode for selenoid
lock | 1 | $0.05 | Link 1 | Amazon/D-PLANET | In Transit | Link 1

### 6 TIP102 Transistor

Switch to enable power to
solenoid | 1 | $1.60 | Link 1 | Amazon/STMelectronics | In Transit | Link 1
7 | 3.7V LiPo | Backup power system | 1 | $13.53 | Link1 | Amazon/Adafruit | In Transit | Link 1
8 | DROK LM2577 DC-DC Booster converter | DC-DC boost converter (3vto12v) to drive the Solenoid | 1 | $15.26 | Link1 | Amazon/Adafruit | In Transit | Link 1

4. Updated Project Schedule | (to be used for monitoring project progress)
Task or Milestone | Semester week
We are adding an emergency power system (schematic) | 4
Implement Wi-Fi bridge between ESP32 and computer | 4
Program ESP32 to trigger solenoid using NFC shield. | 4
Order power system components | 4
Finalize schematic for Smart Doorbell | 5
Program UI for monitoring people traffic through the door | 5
Test power system circuit (emergency as well) | 5
Establish communication with Android app and ESP32 | 6
Work on face recognition algorithm | 6
Implement proximity sensor (algorithm and hardware) | 6
Implement Wi-Fi communication between ESP32 and ESP32-CAM | 7
Keep working on face recognition algorithm | 7
Implement profile database support for Android app to have multiple users | 7
Implement IoT platform to unlock Smart Lock using phone through Wi-Fi | 8
Test face recognition algorithm | 9

Note: Schedule will be updated on week 6 with further information.

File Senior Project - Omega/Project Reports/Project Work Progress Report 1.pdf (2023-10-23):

Project Work Progress Report No 1

Date: 02/10/2019 | Team #: 33
Project Title: Anti-theft Package Security Home System (APSHS)
Submitted by: Gregory Escobar, Stephen Benavides, Shawn Carnevale, Geomar Reyes

### 1. Project progress since last report:

We are currently working with the ESP32-WROOM-32D MCU and the PN532 NFC shield. We are learning how to program them since the ESP32-WROOM-32D arrived on 02/07/2019. We are using these two components to implement the Smart Lock module. This week we are going to keep testing communication between these two components as well as the implementation of a simple LAN network.


Schematic and with the specific pins to accomplish the communication between modules have been finalized.


We are also still designing the extra module added to the project so the project will become more interesting. This module is the Smart Doorbell. Research is being done on how to implement the face recognition algorithm. A proximity sensor has to be implemented to enhance low power consumption by decreasing the time the camera will be on.


Emergency power system has not been designed yet but the hardware group will be designing it during this week.

### 2. Milestones achieved:

- Stablished communication between Adafruit PN532 and ESP32-WROOM-32D using I2C communication protocol 02/10/2019 – Gregory Escobar
- Login screen finalized using Android Studio App 02/08/219 – Geomar Reyes
- ESP32-WROOM-32D was successfully added to a Local Area network (LAN) 02/10/2019 – Stephen Benavides.
- Power supply AC-DC 3.3V power system for Smart Lock module design finalized 02/10/2019 – Shawn Carnevale.

### 3. Problems and roadblocks, if any:

Face recognition algorithms are very complex. Implementation and designing can be a time-consuming process.
ESP32-CAM MCU used to implement the Smart Doorbell Module got backorder which decreases the time to test face recognition.
4. Is project on schedule? | YES__X___ | NO____

5. Next steps: (elaborate specifically on any problems listed in 3 and if the answer in 4. Is NO) (You may use more pages, if needed)
Even though face recognition is a very complex algorithm to implement, there are many resources online that can help us achieve the purpose of our project. There are many libraries on Python that make the implementation of Face recognition much easier. There are many people that have also implemented face recognition with the same module we have ordered and succeed on the process. We are working using these resources and the code can be tested on the MCU we currently have because it is similar to the module that got backordered.

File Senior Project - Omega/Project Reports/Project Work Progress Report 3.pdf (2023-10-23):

Project Work Progress Report No 3

Date: 03/10/2019 | Team #: 33
Project Title: Intelligent Door System
Submitted by Gregory Escobar, Stephen Benavides, Shawn Carnevale, Geomar Reyes

### 1. Project progress since last report:

Hardware
The power system we are designing for our project has been completed and we have all the necessary components. The main issue we had was to find the right boost converter to step up the 5V line to 12V because of the solenoid lock we previously selected while also providing battery backup system when a power outage occurs. We were able to find those components for a very affordable price and because of this it simplified our schematic and design. Our next goal will be to build the power system and test it.


The following two weeks:

- A list of the different GPIOs needed for the project will be finalized by the end of next week.
- Preliminary design of PCB will be finalized.
- Power System will be tested.

Network Framework
- Connection has been made with router in a private network.
- After stablishing the connection, the ESP32 displays the IP address of the private network in the serial monitor, thus allowing us to ping the network easier in order to stablish an internet connection.

- ESP32 Wi-fi capabilities were enabled allowing it to connect multiple devices, the ESP32 will display the number of devices connected in its network.
- A personal IP, gateway and mask were generated in order to create a static IP address for the ESP32, this will come in handy when trying to connect to a server for the App

The following two weeks:

- Create a small web server in LAN
- Generate an access point between the ESP32 and the web server
- Use the Wi-Fi capabilities previously developed in the ESP32 to make it accessible to the web server regardless of the distance
- Generate status messages in the web server though the ESP32. This status will indicate how many devices are connected in the ESP32, the name of the devices and the IP addresses. This will be useful when we trying to encrypt the user’s information for better security.

Application
- Login interface finalized by allowing multiple users to have its own account
- Application is Wi-Fi enabled.
The following two weeks:
- Create a password and encryption method to unlock the door wirelessly using Android App.
- Test Wi-Fi connection and pairing method of the ESP32 with the application.

### 2. Milestones achieved:

- Power System finalized
- MCU Wi-Fi capabilities were enabled
- Application is Wi-Fi enabled
- Account and User interface finalized in Application
- Solenoid circuit has been tested.

### 3. Problems and roadblocks, if any:

- I2C and SPI communication between the ESP32 and PN532 is not possible.
- The ESP32-CAM module for Smart Doorbell module was backordered because they are out of the stock.
4. Is project on schedule? | YES__X__ | NO____
5. Next steps: (elaborate specifically on any problems listed in 3 and if the answer in 4. Is NO)


The Adafruit PN532 was removed from the project because of time constrains. This shield enabled NFC features in the project. The team is going to work in implementing a password and encryption method on the Android App so the lock can be unlocked wirelessly by applying different levels of security. The diagram has been updated.

We are looking into replacing this module by buying this camera (ESP32 compatible) and using the board to communicate with it.

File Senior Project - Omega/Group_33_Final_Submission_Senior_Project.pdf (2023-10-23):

1

### ECE 414 Senior Design Project Proposal

Team number: 33

Project Title: Intelligent Door System (IDS)

Name(s): Shawn Carnevale ID# 31365543 Name(s): Gregory Escobar ID# 31366105 Name(s): Stephen Benavides ID# 31250644 Name(s): Geomar Reyes ID#31009696

2

Abstract
Our project consists of designing an intelligent security door system. The idea behind our project is to create a system that uses an electronic door lock with wireless communication module so that a person in the possession of an NFC device can get access to a secured area. Our project will be designed to provide security to the customer that will buy our product. This security is going to be in the form of a backend server that will make sure that you are authorized to be in a specific area. A mobile phone application or computer software will be used to display any important information and configure the system.

3

Table of Contents

Relevant engendering standards | 5-6
Project constrains | 6-8
Design methodology, analysis, prototyping and validation | 8-11
Project originality | 11-12
Marketability | 13-14
Conclusion | 14-15
References | 16-17

4

Introduction
The ongoing evolution of the network of computing devices embedded in everyday objects to transmit and receive data better known as the Internet of Things (IoT) has enabled devices to become smart objects. New communication interfaces, like Near Field Communication (NFC), have been integrated in different devices. This technology is a type of Radio Frequency Identification (RFID) that could have a great impact on the usability for security systems by enabling the integration of NFC enabled devices to a network and using them as a medium to grant authorization to specific areas. In this context, an emerging trend is the integration of NFC devices like smartphones or just simple tags into modern security systems such as access control lock, unlock and configure the system. In specific, NFC is suitable for this application due to its close-range communication requirement.

In this paper, we propose a simpler way to go in and out into authorized areas by using an Intelligent Door System (IDS). An IDS consist of an electronic door lock that prevents an unknown or restricted person from entering a specific area unless the corresponding tag or token is physically present or authenticated. Access rights can be given to multiple users, cancelled or bound specific levels of security. All this organization and distributions of keys will be done though a software application. Despite of all the advantages of this innovating system, there are certain challenges like security aspects that will have to be target during the designing process.

Technical Goal
1. Select appropriate controller and compatible RFID hardware.

### 2. Design a friendly user interface (tablet, phone, computer) 3. Stablish communication protocols for the systems mentioned above

Roles
- Shawn Carnevale: Hardware implementation and assembly process.
- Stephen Benavides: Network and Communication implementation.
- Gregory Escobar: Software implementation.
- Geomar Reyes: Security (Hardware and Software) implementation.

5

Projected Community Impact
- It will help people with disabilities access the facilities that have been implemented with our device easily as it does not require an external force to open the door.
- Increased security standards at home and businesses by 20% as the device is provided with an automatic closing mechanism.
- Improved response time during emergency situations.
- Allowing quick access to the facilities could increase productivity by 5%.

Relevant ethical issues
In our project we face some ethical concern with the security of our product. The main

ethical concern is people’s privacy. Privacy can be described as a person right to keep their

information from being public. The main ethical impact is going to occur on the gathering,

storage, retrieval and dissemination and the impact relate to accessibility/inaccessibility and the

manipulation of information. Because a lot of different people have access to this system the risk

of information getting stolen or use for the wrong purpose increase. We can prevent this from

happening by implementing security measure like password and other security measure we can

implement to make sure that just the right people have access to sensitive information.

Engineering standards
The project consists of electrical hardware that will use wireless communication to receive and send data between different devices. The project must comply with the IEEE, NFC Forum and FCC signal and frequency standards.
- IEEE 802.11: This standard deals with wireless communication between devices. There are a set of Media Access Control (MAC) and Physical layer used for implementing wireless local area network. This apply to this project because there is an electronic door lock that will communicate wirelessly to a computer and to a NFC enable device or tag. The FCC 1934 act “title” deals with the regulation of all wireless communication from

6

telecommunication to microwave and many other types of wireless communication. This will be critical because things like wireless communication and RF signal are regulate by this industry for safety of and public.
- ISO/IEC 14443: This standard defines proximity cards used for identification, and the transmission protocols for communicating with it.
- ISO/IEC 18092:2013: This standard defines communication modes for Near Field Communication Interface and Protocol (NFCIP 1) using inductive coupled devices operating at the center frequency of 13,56 MHz for interconnection of computer peripherals. It also requires conditions to control data collisions when transmitting data.
- Unfortunately, there are no standards regarding data management. The project will be handling sensitive information about a person or a company. The system will be designed to prevent any alteration or any unauthorized access to this information.

Constrains:
Legal:
- The components use for our device are open source, they can be acquired from the company and be use freely in the implementation of our device, thus avoiding legal problems when the project is released to the market.
- Whenever we are talking about someone’s personal information, legal issues are always important to address.
- When working with people’s personal information we must provide confidentiality and protection, otherwise we might get some legal issues and more importantly we will lose people’s trust in our device.

Confidentiality Agreement: The information provided by the user will be encrypted and their personal information such as names won’t be listed in our database giving the user the anonymity status.

Protection Policy: The information provided by the user won't be share to a third party unless requested by a higher authority. The information won’t be made public by the company under

7

any circumstances. By disclosing legal issues, we will avoid any legal action towards the company and its associates.

Budget:
One of our biggest challenges is going to be to create our project for the least amount of money but also work efficiently. This is always an important question whenever an engineer works in the industry because time is money. We have determined that the programming and the Arduino chip will not cost that much money but, the linear actuator and the bracelet could be big factors in the price. The following table shows the equipment that will have to be purchased to start developing the project.
Item | Price
Linear Actuator L16 | $79.99
Rutherford Electric Strike Electronic Lock | $59.68
Adafruit PN532 NFC/RFID | $39.95
DC Power Supply | $10.00
Door Hinges | $7.98
NTAG213 by Tagstand NFC tags | $9.99
1740 Adafruit Speaker | $0.95
Total Price | $208.54

Technical Constraints:
- Since we are using NFC technology which is a branch of HF RFID (13.56MHz) the maximum range will be 10cm (4 inches). The NFC shield should be placed close enough

8

to the door knob and make sure that there isn’t a metal barrier that will attenuate the radio wave.
- Providing enough power to trigger the linear actuator in order to open the door.

Design methodology, analysis, prototyping and validation.


Design Objectives, Requirement, Specification
The design objective is to create an intelligent door system that will use a wireless communication module so that a person in the possession of an NFC (Near Field Communication) device can get access to a secured area.

Benchmarking
This device will provide a quicker, cheaper and more reliable way to protect and access facilities in comparison with other similar systems. For instance ID card for doors requires of expert installation and electrical wiring to control the locking mechanism of the door, the cards itself can be lost or stolen easily and the mass production of this card can cause serious harm to the environment in the long term, in comparison our system is easy to install by the end user, the NFC transmitter can be implemented in any personal belonging of the user, as well as a virtual key

9

for your phone thus making it harder to lose or forget and easier to access, because the “key” for the NFC transmitter can be implement to the phone through software it will leave a leaser carbon foot print thus helping the environment.

Design Concept and Constraints
It’s a dispositive that will open the door after receiving a signal from the NFC transmitter, this will in return send a signal back to the servers to prove its validity. Since we are using NFC technology which is a branch of HF RFID (13.56MHz) the maximum range will be 10cm (4 inches). The NFC shield should be placed close enough to the door knob and make sure that there isn’t a metal barrier that will attenuate the radio wave. We will also have to make sure that enough power is provided to trigger the linear actuator to open the door.

Business and Economic Perspectives
Our design is of cheap production, we use open source software and hardware, thus making it viable for mass production, this in exchange will allow us to sell it for a significant profit. The easy installation will provide a better response from the community making it accessible not only to companies but also regular homes.

Software Design
The Arduino program interface will provide an access point between the NFC receiver and transmitter, when the user attempts to access the facility though the IDS (Intelligent Door System) this will send a signal to the door, the door will access the database to confirm the user identity, if the user is authenticated the door will open and the user will be able to access the facility. If the user information is not in the database, then access will be denied. In both cases the main user will be notified in the correspondent software.


10

Hardware Design

11

Prototyping, Testing and Integration
For our project we are going to build a small model that can be used on a bigger scale. The block diagram shows how our project works and how the components interact with one another. The model we are going to build is quite simple with only a few components. First, we are going to attach the linear actuator, the Arduino, the power source and the alarm to a plank of wood. Then we are going to build a 12x8 box made of wood with one end open with a piece of wood attached to hinges. Since the linear actuator can extend a total of seventeen inches we want to make the box smaller so the movable end of the box can open. Our prototype can be thought of as a security box. When the RFID/NFC comes close to the box if they are authorized the actuator will extend and open. If the person is not authorized an alarm will go off.

Prototype Assembly
To build our project we are first going to use a table saw to cut precise planks of wood for our box. Next, we are going to drill screws into the planks of wood, so they don’t come apart. The next thing we must do is cut a hole in the back, so we can run the power supply cable to the linear actuator and Arduino. After we cut the hole in the back and run the power cables, we are going to drill hinges to the front of the box and attach a piece of wood to them, so the box can open and close. When we start to build the project there still are some questions. One of the questions is how thick each plank of wood should be. We want our model to be as compact as possible but also sturdy. Another question is do we attach the actuator on top or the bottom of the box. The last question is if we are going to use an extension cord for our power supply. Depending on how far the box is from the wall will it be necessary. These are questions that will be answered when we start to physically build our project.

Project Originality
The Intelligent Door System (IDS) has a lot of competition in the current security market. The Smart lock systems and methods (patent number: US8947530B1) is a lock that can receive electricity from a transformer of a doorbell chime while the lock is mounted on a door. This system uses facial recognition feature that can be expensive to implement and can have a high probability of error because it is an emerging technology. This smart lock is selling for a very high price in amazon. This patent was invented by Joseph Frank Scalisi. In contrast, our system

12

takes advantage of Near Field Communication (NFC) which is less expensive and easier to implement. In our project we will have a phone that is NFC enabled, which will allow us to open the door without touching the lock or without having a key. This patent just uses a mobile app in contrast with the IDS which also has a PC application that will allow companies to install it in different computers for a better security protocol throughout all the company.

The Gate Smart Lock is also another smart lock (patent number is US20140265359A1). The Gate smart lock is a smart Wi-Fi door lock with a built-in camera that records video when somebody approaches it. This lock is using motion detection which is very expensive to implement compared to an NFC module. In addition, it will end up consuming more cache memory because it will be recording video thus restricting the functionality of the lock. In comparison the Intelligent Door System (IDS) will only use signals when the knob is used, and because we are not using video but logs data instead, our system will be more reliable and faster, and will consume less energy thus making it energy efficient. The Gate Smart Lock doesn’t have an integrated software that will allow you to have different levels of security within a facility in comparison the Intelligent Door System (IDS) has an interface that will provide the user to program different levels of security for different access points. Our system has an automatic linear actuator which will automate the opening of the door. In conclusion, the Intelligent Door System (IDS) provides a better interface, versatility and reliability when accessing the different facilities.

In the paper, ‘Near Field Communication’ by Tomi Aarnio the author explains how Near field communication (NFC) has many applications when it comes to security systems. The reason being is because for the sensor to read the person’s information he/she has to be close. When reading an article where about NFC communication more in depth we realized that NFC sensors typically consume little power and tend to be cheaper as well. For our project NFC sensors was the best for us to use because of its wide use in any type of security system. Because of it low power consumptions the components don’t have to be that big either which greatly simplified our project.

13

Marketability:
This product targets companies and home owners. It will serve the consumer as an automated security system. This will be achieved by taking advantage of the internet of things. This will allow users to have more control over a specific area. There are several smart lock systems in the market that provide similar services to this product, but the difference is that we are taking the advantage of NFC technology in conjunction with IoT network of devices that allow the user to have a better perspective of the flow of people to specific areas. The competition for our product is the Kitwest Kevo smart door lock. This lock has a lot of the same feature that we want to implement into our project, but our product will have the latest innovation when it come wireless communication. Also, another competitor that we have is Gate Smart Lock which have a camera integrate to it and can be control though an app. Our competitor price is $500, but our product will be market between $350 to $400. Intelligent Door System is a system that will be relevant in the current market.

Proposed 414-416/417 timeline and milestones


Time Range | Task
1/1 – 1/7 | Place order of Equipment
1/8 – 1/14 | Test Functionality of Equipment
1/15 - 1/20 | Get the NFC Shield to write/read NFC device or tag GUI template starts
1/21 – 1/27 | Start framework communication between Arduino and PC station or mobile Device

14

1/28 – 2/4 | Test data transmission between Arduino and mobile or PC
2/5 – 2/12 | Integrate database to the network. Get Arduino to trigger linear actuator and electronic lock
2/13 – 2/20 | Test NFC device read/write in conjunction with linear actuator trigger after authentication
2/22 – 3/1 | Attach electronic lock to the system. Test time delay of door unlock and linear actuator
3/2 – 3/12 | GUI finalized for desktop application GUI for mobile app starts
3/13 – 3/21 | Integrate small touch screen panel of locking door from inside. Integrate door bell for visitors
3/23 – 3/30 | Test mobile application add camera for security purpose
4/1 – 4/10 | Implement security protocols to the system and test them
4/12 – 4/21 | Final test deployment of project

Conclusion
In the proposed project, we designed a system comprised of an electronic door lock with wireless communication module so that a person in the possession of an NFC device can get access to a secured area.
We performed a research making emphasis on how to improve the life of the user while making it easy to use and buy. After a long research and spending time deliberating, we decided to design the Intelligent Door System (IDS). The IDS will give the user an improved accessibility and security that until now was reserved for extremely important facilities that needed to protect sensible places. But now the same level of security and accessibility can be given to anyone by a fraction of the price.
We concluded that the proposed system will vastly improve security and accessibility thus having a high probability of replacing current security measures such as ID cards readers for doors.

15

Because our system is going to be of easy installation and lower cost in comparison to the competition. It’s more likely to not only succeed in places that requires high security systems such as governmental offices but also in the common households that seeks an improved and cheaper security measure.

16

References
802.15.3-2016 - IEEE Standard for High Data Rate Wireless Multi-Media Networks, IEEE Xplore. Retrieved November 6, 2018 from https://ieeexplore.ieee.org/document/7524656

Arduino UNO SD, Arduino. Retrieved November 18, 2018 from https://www.arduino.cc/en/Main/ArduinoBoardUnoSMD

Doorbell communication systems and methods, Google Patents. Retrieved November 15, 2018 from
https://patents.google.com/patent/US8780201B1/en?inventor=Joseph+Frank+Scalisi

Intelligent Door Lock System, Google Patents. Retrieved November 7, 2018 from https://patents.google.com/patent/US20140265359A1/en.

ISO/IEC 14443, (n.d.) Retrieved October 30, 2018 from https://en.wikipedia.org/wiki/ISO/IEC_14443

ISO/IEC 18092:2013, (n.d.) Retrieved November 5, 2018 from https://www.iso.org/standard/56692.html

Near Field Communication, Tomi Aarnio, Aalto University. Retrieved November 15, 2018 from https://users.aalto.fi/~anttiyj/msc-thesis/2013-msc-tomi-aarnio.pdf

NFC Forum, (n.d.) Retrieved October 24, 2018 from https://nfc-forum.org/?s=Data+standards

Near Field Communication in the real world, Innovision Research & Technology plc. Retrieved October 29, 2018 from
https://members.nfcforum.org/resources/white_papers/Innovision_whitePaper1.pdf

17

Read and Write on NFC Tags with an Arduino, All About Circuits. Retrieved on September 30, 2018 from https://www.allaboutcircuits.com/projects/read-and-write-on-nfc-tags-with-an-arduino/

18

Appendix
Read and Write on NFC tags code:

void setup(void) {
Serial.begin(9600);
Serial.println("NFC TAG READER"); // Header used when using the serial monitor nfc.begin();
}

void loop(void) {
Serial.println("\nScan your NFC tag on the NFC Shield\n"); // Command so that you an others will know what to do

if (nfc.tagPresent())
{
NfcTag tag = nfc.read();
Serial.println(tag.getTagType());
Serial.print("UID: ");Serial.println(tag.getUidString()); // Retrieves the Unique Identification from your tag

if (tag.hasNdefMessage()) // If your tag has a message
{

NdefMessage message = tag.getNdefMessage(); Serial.print("\nThis Message in this Tag is "); Serial.print(message.getRecordCount()); Serial.print(" NFC Tag Record");
if (message.getRecordCount() != 1) { Serial.print("s");
}
Serial.println(".");

// If you have more than 1 Message then it wil cycle through them int recordCount = message.getRecordCount();
for (int i = 0; i < recordCount; i++)
{
Serial.print("\nNDEF Record ");Serial.println(i+1); NdefRecord record = message.getRecord(i);

int payloadLength = record.getPayloadLength(); byte payload[payloadLength];
record.getPayload(payload);

String payloadAsString = ""; // Processes the message as a string vs as a HEX value for (int c = 0; c < payloadLength; c++) {
payloadAsString += (char)payload[c];
}
Serial.print(" Information (as String): "); Serial.println(payloadAsString);

String uid = record.getId();
if (uid != "") {
Serial.print(" ID: ");Serial.println(uid); // Prints the Unique Identification of the NFC Tag }
}
}
}
delay(10000);
}

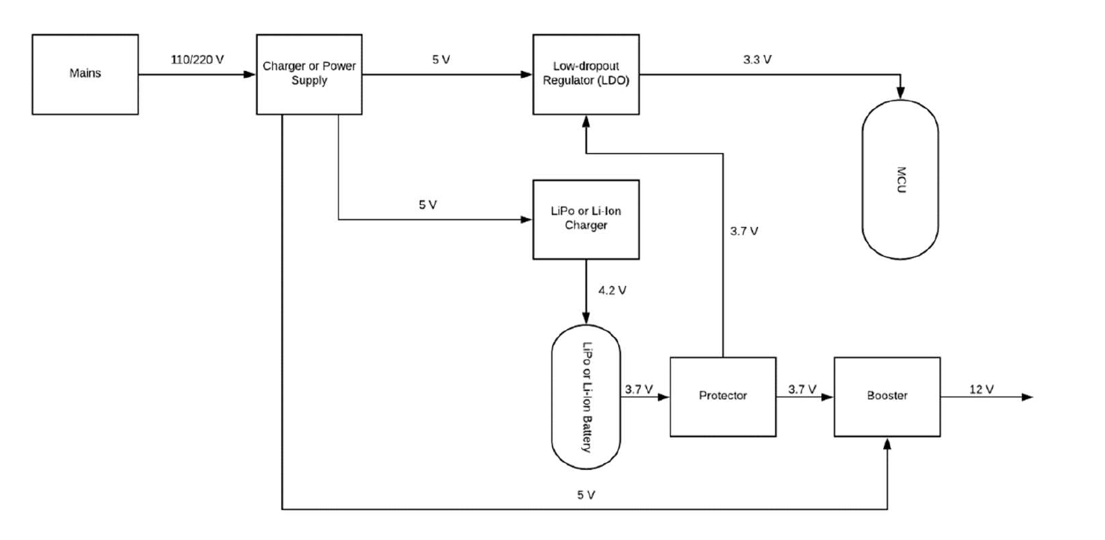
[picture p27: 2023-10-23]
Senior Project - Beta/Smart Lock (Pending Name)-20201122T195937Z-001/Smart Lock (Pending Name)/Schematics/Screen Shot 2019-09-06 at 3.22.17 PM.png

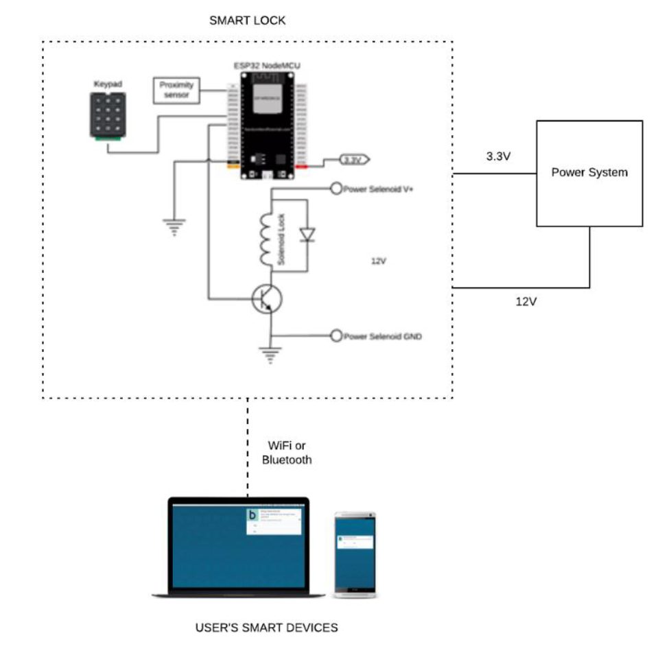
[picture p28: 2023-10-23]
Senior Project - Beta/Smart Lock (Pending Name)-20201122T195937Z-001/Smart Lock (Pending Name)/Schematics/Screen Shot 2019-09-06 at 3.26.19 PM.png

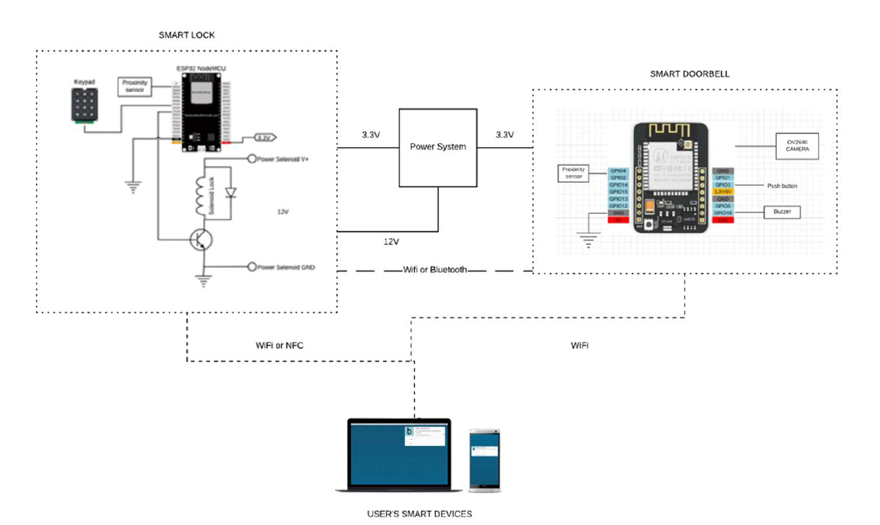
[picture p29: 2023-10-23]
Senior Project - Beta/Smart Lock (Pending Name)-20201122T195937Z-001/Smart Lock (Pending Name)/Schematics/Screen Shot 2019-09-06 at 3.23.36 PM.png

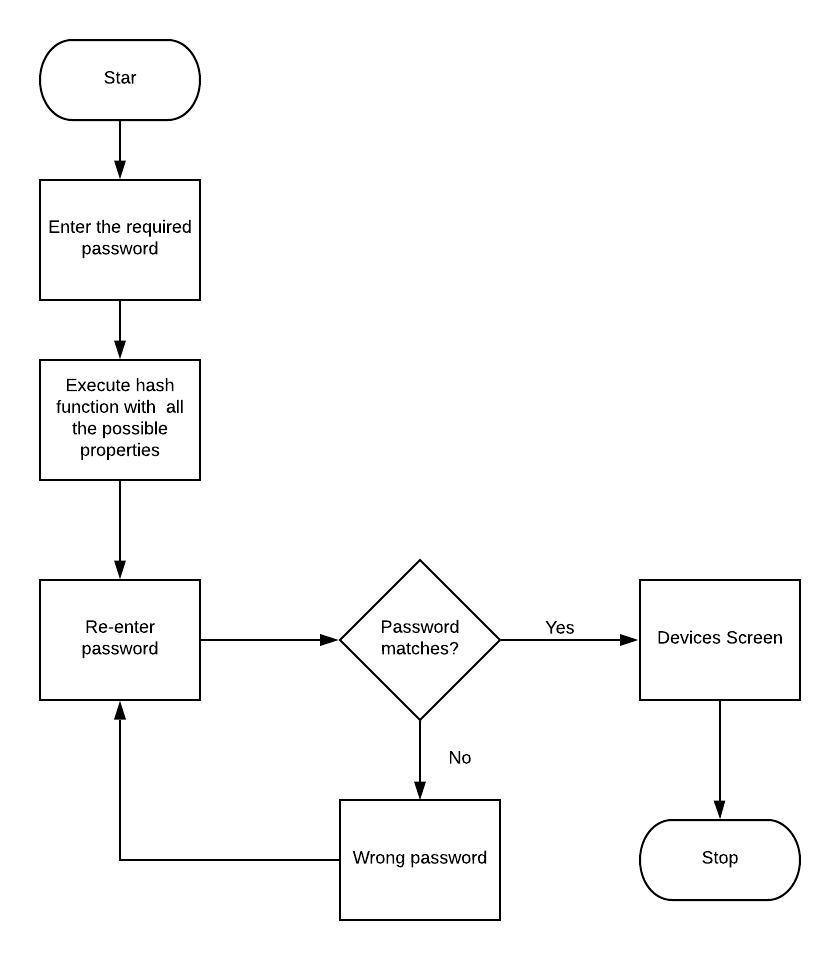
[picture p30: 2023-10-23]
Senior Project - Beta/Smart Lock (Pending Name)-20201122T195937Z-001/Smart Lock (Pending Name)/Software/Algorithm security (1).jpeg

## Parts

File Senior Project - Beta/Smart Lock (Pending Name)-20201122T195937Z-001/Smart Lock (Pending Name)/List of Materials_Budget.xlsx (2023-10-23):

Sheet: Main Budget
 | Name | Description | Quantity | Price | Link | Distributor | Status | Specs/Datasheet | Notes:
2 | SLNDLTCH12 12V Electronics Lock Assembly Solenoid Low Power Consumption | Electric lock for the door | 1 | $17.61 | Link 1 (https://www.amazon.com/Adafruit-Lock-style-Solenoid-12VDC-ADA1512-x/dp/B01GQFUQ06) | Amazon/Adafruit | Received on 01/19 | Link 1 (https://www.adafruit.com/product/1512)
3 | ESP32-WROOM-32D / DEV module | Microcontroller with WiFi capabilities like the ESP8266 | 2 | $11 | Link 1 (https://www.amazon.com/HiLetgo-ESP-WROOM-32-Development-Microcontroller-Integrated/dp/B0718T232Z?s=pc) | Amazon/Hitlego | Received on 01/31/19 | Link 1 (https://www.espressif.com/sites/default/files/documentation/esp32_datasheet_en.pdf)
 |  |  |  |  |  |  |  | Link 2 (https://docs.espressif.com/projects/esp-idf/en/stable/)
 |  |  |  |  |  |  |  | Link 3 (https://www.espressif.com/sites/default/files/documentation/esp32-wroom-32d_esp32-wroom-32u_datasheet_en.pdf)
 |  |  |  |  |  |  |  | Link 4 (https://github.com/espressif/arduino-esp32)
5 | 1N4004 Diode | Protection diode for selenoid lock | 1 | $0.05 | Link 1 (https://www.amazon.com/100pcs-1N4004-Diode-Standard-Through/dp/B07J58K2RZ?s=industrial) | Amazon/D-PLANET | Received 02/07/19 | Link 1 (https://www.onsemi.com/pub/Collateral/1N4001-D.PDF)
6 | TIP102 Transistor | Switch to enable power to solenoid | 1 | $1.60 | Link 1 (https://www.amazon.com/STMICROELECTRONICS-TIP102-TRANS-DARL-pieces/dp/B00M1GGKIC) | Amazon/STMelectronics | Received 02/07/19 | Link 1 (https://www.mouser.com/datasheet/2/389/tip102-957196.pdf)
9 | Uninterruptible Power Supply | Power System | 1 | $3 | Link 1 (https://www.amazon.com/Makerfocus-Battery-Shield-Raspberry-Arduino/dp/B075HB98J9) | Amazon/MakerFocus | Received 02/20/19
 |  |  |  |  | Link 2 (https://www.aliexpress.com/item/ESP32-ESP32S-For-Wemos-For-Raspberry-Pi-18650-Battery-Charge-Shield-Board-V3-Micro-USB-Port/32870411748.html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)
10 | DC-DC boost converter | DC-DC Boost converter | 1 | $13 | Link 1 (https://www.amazon.com/Converter-DROK-Buck-Boost-Adjustable-Regulator/dp/B0789QVKKF?s=gateway) | Amazon/Drok | Received 03/09/19
11 | Keypad | 3x4 Phone-style Matrix Keypad (i2c) | 1 | $11 | Link 1 (https://www.amazon.com/Adafruit-3x4-Phone-style-Matrix-Keypad/dp/B00QSHPCO8) | Amazon/Adafruit | Received 03/15/19 | Link1 (https://www.adafruit.com/product/1824) | 8 pin
12 | Single Pole Double Throw Switch 400UDP1R1BLKM7RE | M7 Rocket model | 2 | $1.62 | Link 1 (https://www.mouser.com/ProductDetail/E-Switch/400UDP1R1BLKM7RE) | Mouser Electronics | Received 03/25/20 | Link 1 (https://www.mouser.com/datasheet/2/140/400U-837934.pdf) | We are using M7 Rocket model (6 pin)
13 | Male connector JST-PH 2-pin |  | 3 | $0.75 | Link 1 (https://www.mouser.com/ProductDetail/Adafruit/1769?qs=sGAEpiMZZMsMyYRRhGMFNlCdtNxpnOUdaNxuf4VjKxc%3D) | Mouser Electronics | Received 03/25/21 | Link 1 (https://www.adafruit.com/product/1769)
14 | RGB LED WP154A4SUREQBFZGC |  | 2 | $1.88 | Link 1 (https://www.mouser.com/ProductDetail/Kingbright/WP154A4SUREQBFZGC) | Mouser Electronics | Received 03/25/22 | Link 1 (https://www.mouser.com/datasheet/2/216/WP154A4SUREQBFZGC-1173568.pdf) | 4 pin
15 | Pushbutton |  | 5 | $0.21 | Link 1 (https://www.mouser.com/ProductDetail/Grayhill/95C06C3RAT?qs=ls7QRyWmRk4CrjuiuVECkg%3D%3D) | Mouser Electronics | Received 03/25/23 | Link 1 (https://www.mouser.com/datasheet/2/626/Tact_95C06-335474.pdf)
16 | Female Headers |  | 2 | $4.00 | Link 1 (https://www.amazon.com/Adafruit-36-pin-0-1-Female-header/dp/B01LYGUT2I) | Amazon/Adafruit | Received 03/25/24 | Link 1 (https://cdn-shop.adafruit.com/datasheets/00548.pdf)
17 | PCB Board |  | 5 | $30
18 | 3D Print box |  | 1 | $8.00

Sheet: Removed Components
 | Name | Description | Quantity | Price | Link | Distributor | Status | Specs/Datasheet | Notes:
1 | L12-R Micro Linear Actuator - Arduino compatible | Linear actuator to open the door | X | $69.99 | Link 1 100mm 210:1 (https://www.amazon.com/L12-Linear-Servo-Motor-Compatible/dp/B0764LHFV5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) | Amazon/Actuonix | Need to review this part | Link 1 (https://images-na.ssl-images-amazon.com/images/I/81luRDw1PwL.pdf) | We need to figure out the force/speed and length needed for our project. Proffessor reoved this part from our project
 |  |  |  |  | Link 1 50mm 210:1 (https://www.amazon.com/L12-Linear-Servo-Motor-Compatible/dp/B0764KZPS7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) |  | Need to review this part
 |  |  |  |  | Link 1 30mm 210:1 (https://www.amazon.com/d/Linear-Actuators/Linear-Servo-Motor-Stroke-18lbs/B0764JWHCQ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) |  | Need to review this part
 |  |  |  |  | Link 1 100mm 100:1 (https://www.amazon.com/Linear-Servo-100mm-9lbs-Force/dp/B074H9HND6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) |  | Need to review this part | Link 2 (https://www.actuonix.com/L12-Micro-Linear-Actuators-s/1821.htm)
 |  |  |  |  | Link 1 50mm 100:1 (https://www.amazon.com/Linear-Servo-50mm-9lbs-Force/dp/B074H7TW2G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) |  | Need to review this part
 |  |  |  |  | Link 1 30mm 100:1 (https://www.amazon.com/Linear-Servo-30mm-9lbs-Force/dp/B074GJSPDC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) |  | Need to review this part
2 | ESP8266 | WiFi module to add network framework | X | $8.40 | Link 1 (https://www.amazon.com/HiLetgo-Internet-Development-Wireless-Micropython/dp/B010O1G1ES) | Amazon/Hitlego | Need to review this part | Link 1 (https://www.espressif.com/sites/default/files/documentation/0a-esp8266ex_datasheet_en.pdf)
3 | ARDUINO UNO R3 [A000066] | Main controller unit (MCU) of the lock | 1 | $19.99 | Link 1 (https://www.amazon.com/Arduino-A000066-ARDUINO-UNO-R3/dp/B008GRTSV6) | Amazon/Arduino | Received on 01/19 | Link 1 (https://store.arduino.cc/usa/arduino-uno-rev3)
4 | Voltage Regulator (LD1117V33) | Regulates the Voltage to 3.3V | X | $1.95 | Link 1 (https://www.sparkfun.com/products/526) | Spark Fun
7 | 3.7V LiPo | Back up power system | X | $13.53 | Link1 (https://www.amazon.com/dp/B0798GYVCW/ref=psdc_10112773011_t2_B0137IPVY6) | Amazon/Adafruit | Return | Link 1 (https://cdn-shop.adafruit.com/datasheets/785060-2500mAh_specification_sheet.pdf) | Protection already included
7 | DROK LM2577 DC-DC Booster converter | DC-DC boost converter (3vto12v) to drive the Solenoid | 1 | $15.26 | Link1 (https://www.amazon.com/DROK-Converter-Adjustable-Voltage-Regulator/dp/B00C9179WK) | Amazon/Adafruit | Received 02/07/19 | Link 1 (https://www.droking.com/dc-dc-lm2577-boost-converter-3-34v-to-4-35v-low-ripple-boost-converter-module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) | Boost the battery voltage to drive the solenoid
4 | ESP32 - CAM | WiFi module for Smart Doorbell | 1 | $7.50 | Link 1 (https://usa.banggood.com/Geekcreit-ESP32-CAM-WiFi-+-Bluetooth-Camera-Module-Development-Board-ESP32-With-Camera-Module-OV2640--p-1394679.html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) | Banggood/Geekcreit | In Transit | Link 1 (https://www.makerfabs.com/desfile/files/ESP32-CAM%20Product%20Specification.pdf) | Migth need another IDE enviroment
 |  |  |  |  |  |  |  | Link 2 (https://github.com/donny681/ESP32_CAMERA_QR)
 |  |  |  |  |  |  |  | Link 3 (https://github.com/donny681/ESP32_CAMERA_QR)
5 | Right Angle Pushbutton |  |  |  | Link 1 (https://www.amazon.com/uxcell-Momentary-Tactile-Button-Switch/dp/B008420Z9W)
1 | Adafruit PN532 NFC/RFID Controller Shield for Arduino | Shield for the arduino to enable NFC | 1 | $39.95 | Link 1 (https://www.amazon.com/gp/product/B00IQY2P82/ref=ox_sc_act_title_1?smid=A19MRELPGC5OXX&psc=1) | Amazon/Adafruit | Received on 01/19 | Link 1 (https://cdn-learn.adafruit.com/downloads/pdf/adafruit-pn532-rfid-nfc.pdf)
 |  |  |  |  |  |  |  | Link 2 (https://learn.adafruit.com/adafruit-pn532-rfid-nfc/overview)
 |  |  |  |  |  |  |  | Link 3 (https://github.com/adafruit/Adafruit-PN532)
13 | OV7670 300KP VGA Camera Module | Camera for the Smart Doorbell | 1 | $11 | Link 1 (https://www.amazon.com/OV7670-Compatible-Arduino-Atomic-Market/dp/B00TKXAGZM) | Amazon/Atomic Market | In Transit | Link 1 (http://www.haoyuelectronics.com/Attachment/OV7670%20+%20AL422B%28FIFO%29%20Camera%20Module%28V2.0%29/OV7670%20Implementation%20Guide%20%28V1.0%29.pdf)
 |  |  |  |  |  |  |  | Link 2 (http://www.haoyuelectronics.com/Attachment/OV7670%20+%20AL422B%28FIFO%29%20Camera%20Module%28V2.0%29/OV7670%20Implementation%20Guide%20%28V1.0%29.pdf)
 |  |  |  |  |  |  |  | Link 3 (http://www.arducam.com/products/camera-breakout-board/0-3mp-ov7670/)

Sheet: References
References: | https://www.youtube.com/watch?v=joAkJ9QA2bw | Emergency Power sys.
Key Pads | https://www.sparkfun.com/products/14836

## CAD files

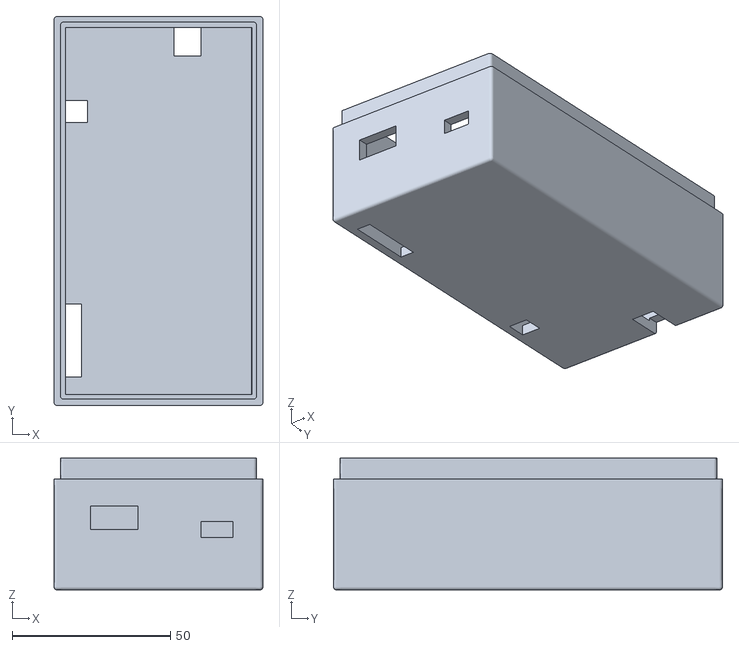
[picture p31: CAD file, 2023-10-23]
Senior Project - Beta/Smart Lock (Pending Name)-20201122T195937Z-001/Smart Lock (Pending Name)/Hardware/CAD model/Half Box Correct.stl
66.0 x 122.9 x 41.7

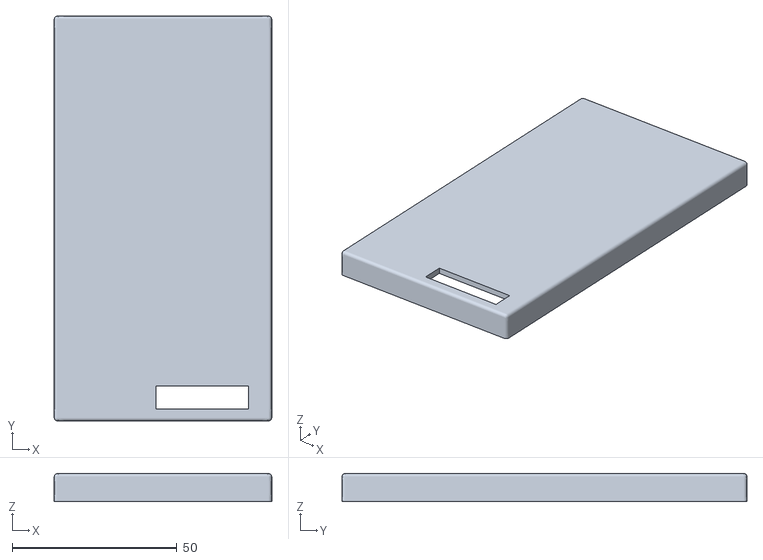
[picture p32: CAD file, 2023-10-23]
Senior Project - Beta/Smart Lock (Pending Name)-20201122T195937Z-001/Smart Lock (Pending Name)/Hardware/CAD model/Smart Lock Box Top Correct.stl
66.0 x 122.9 x 8.50

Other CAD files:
Senior Project - Beta/Smart Lock (Pending Name)-20201122T195937Z-001/Smart Lock (Pending Name)/Hardware/CAD model/Full Box.iam
Senior Project - Beta/Smart Lock (Pending Name)-20201122T195937Z-001/Smart Lock (Pending Name)/Hardware/CAD model/Full box Corect.iam
Senior Project - Beta/Smart Lock (Pending Name)-20201122T195937Z-001/Smart Lock (Pending Name)/Hardware/CAD model/Half Box Correct.iam
Senior Project - Beta/Smart Lock (Pending Name)-20201122T195937Z-001/Smart Lock (Pending Name)/Hardware/CAD model/OldVersions/Full Box.0003.iam
Senior Project - Beta/Smart Lock (Pending Name)-20201122T195937Z-001/Smart Lock (Pending Name)/Hardware/CAD model/OldVersions/Full box Corect.0002.iam
Senior Project - Beta/Smart Lock (Pending Name)-20201122T195937Z-001/Smart Lock (Pending Name)/Hardware/CAD model/OldVersions/Half Box Correct.0001.iam
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

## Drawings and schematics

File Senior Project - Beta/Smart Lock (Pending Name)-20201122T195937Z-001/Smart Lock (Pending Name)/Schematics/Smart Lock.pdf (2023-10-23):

# Power System

1k U10

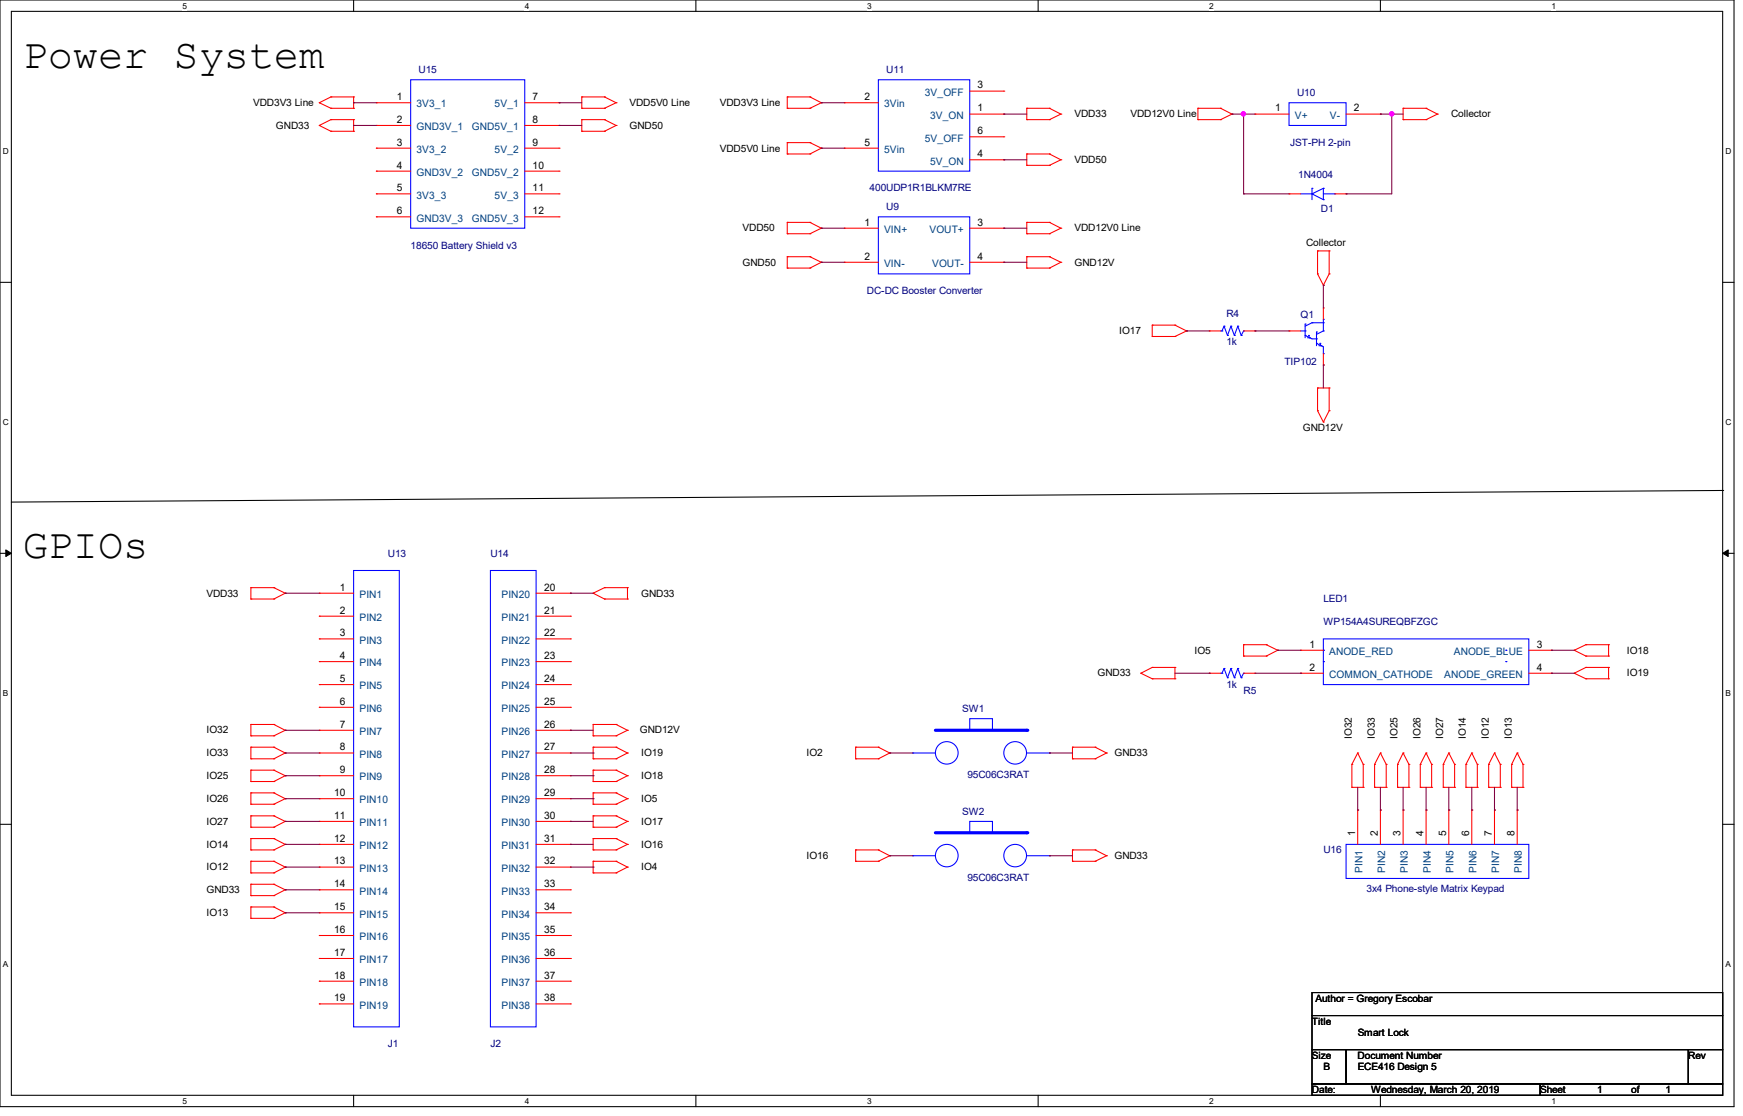
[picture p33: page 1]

1 PIN2
3x4 Phone-style Matrix Keypad PIN¹

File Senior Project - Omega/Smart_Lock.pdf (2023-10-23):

# Power System

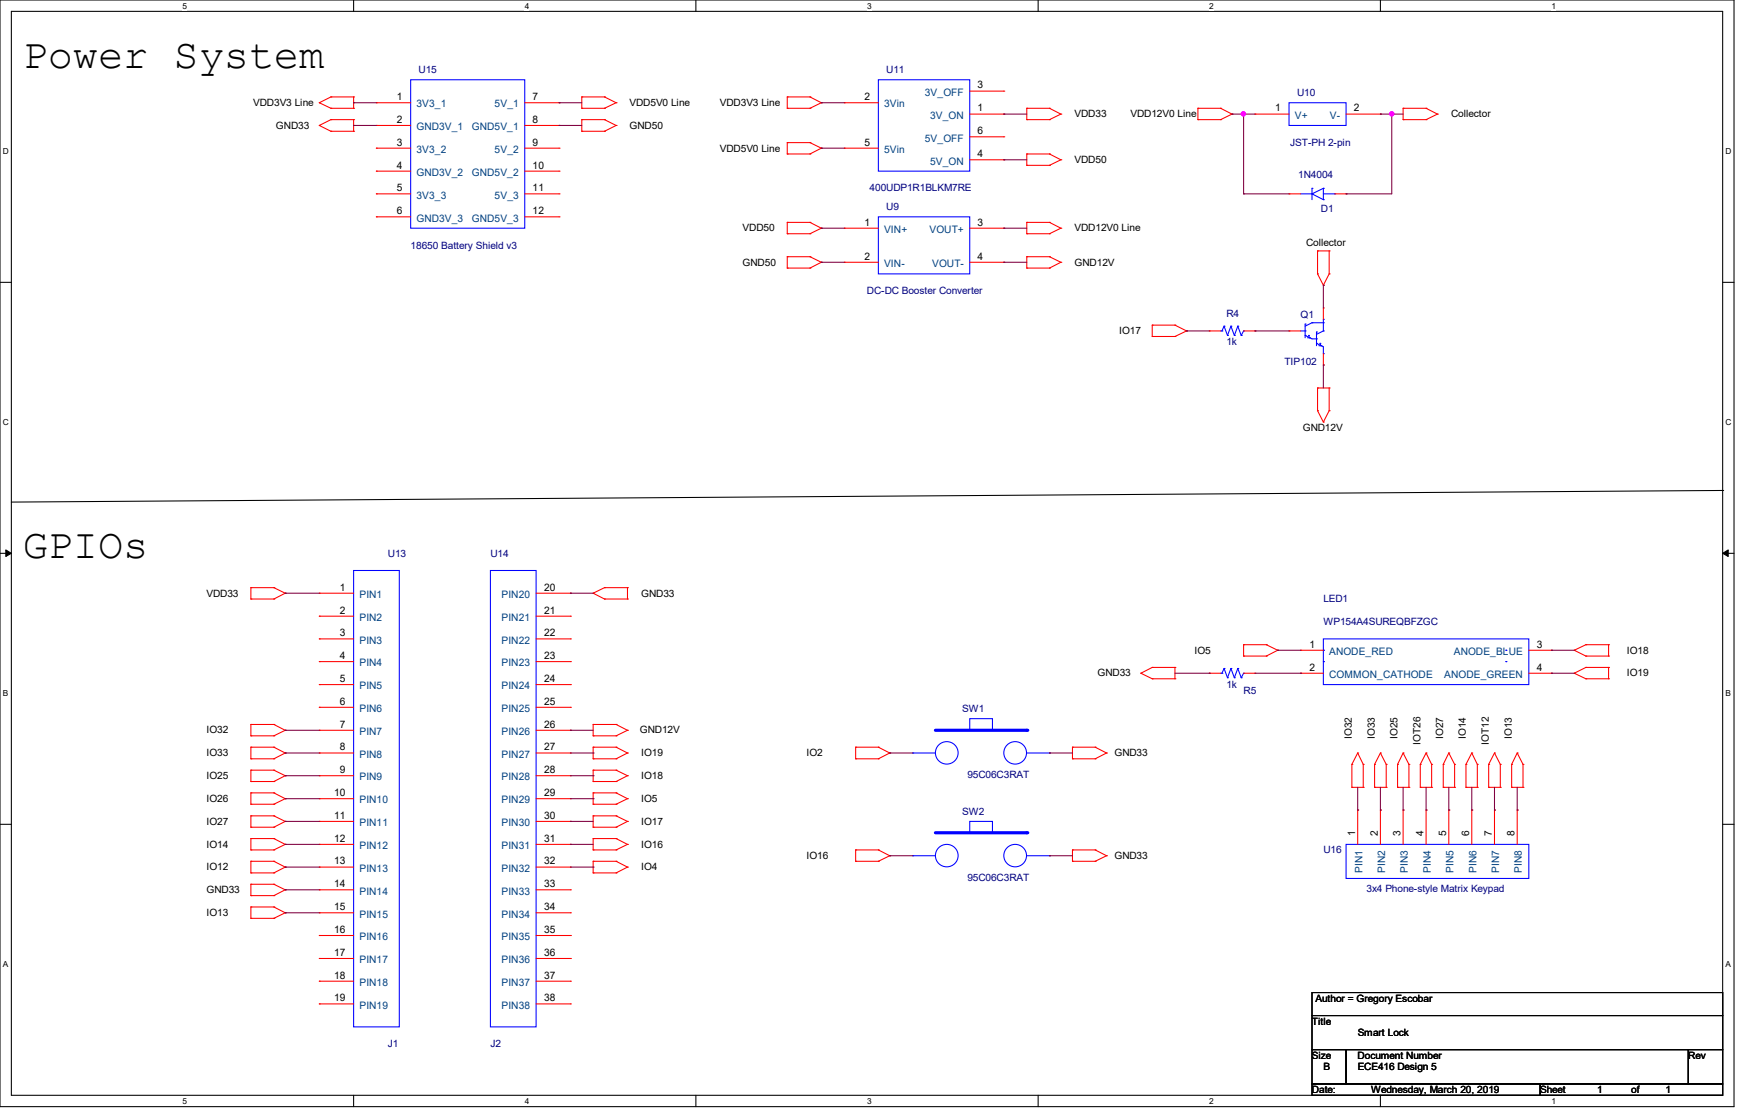
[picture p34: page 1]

1 PIN2
3x4 Phone-style Matrix Keypad PIN¹

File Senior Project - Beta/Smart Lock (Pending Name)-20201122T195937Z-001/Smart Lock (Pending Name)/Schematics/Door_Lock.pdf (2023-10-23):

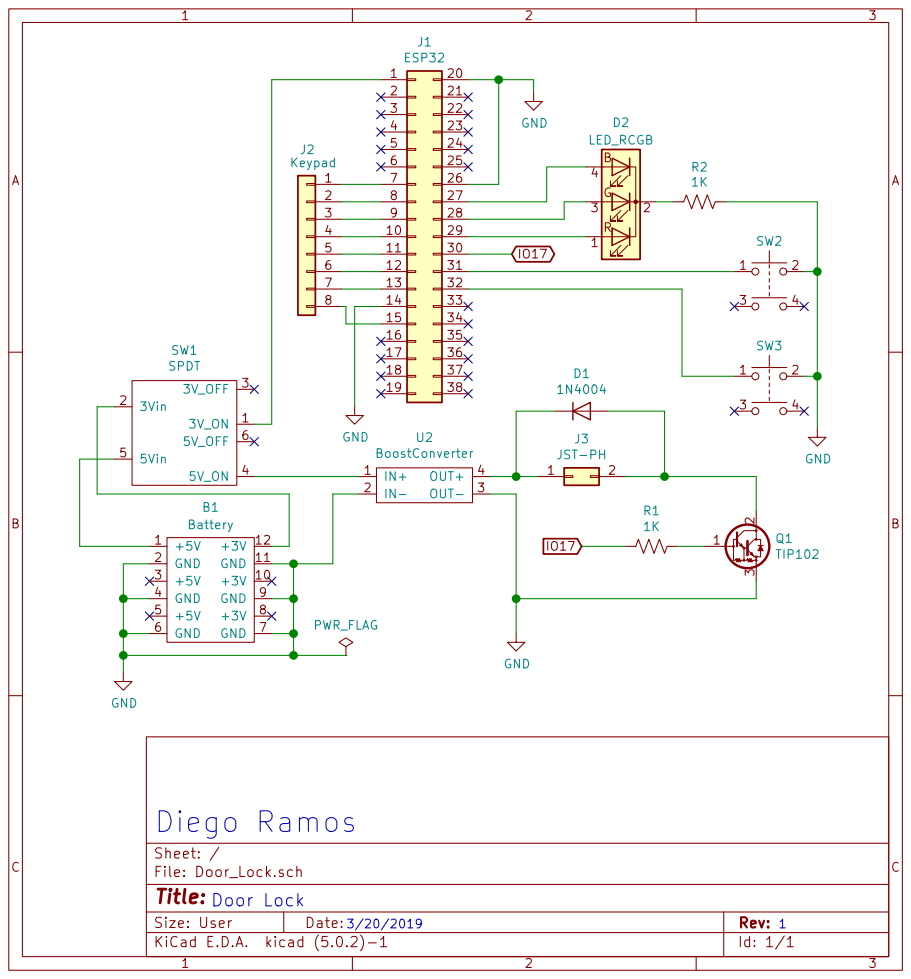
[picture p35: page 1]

2 8 | 27
3 9 | 28
4 10 | 29
5 11 | 30
6 12 | 31
7 13 | 32
8 14 | 33

15 | 34
16 | 35

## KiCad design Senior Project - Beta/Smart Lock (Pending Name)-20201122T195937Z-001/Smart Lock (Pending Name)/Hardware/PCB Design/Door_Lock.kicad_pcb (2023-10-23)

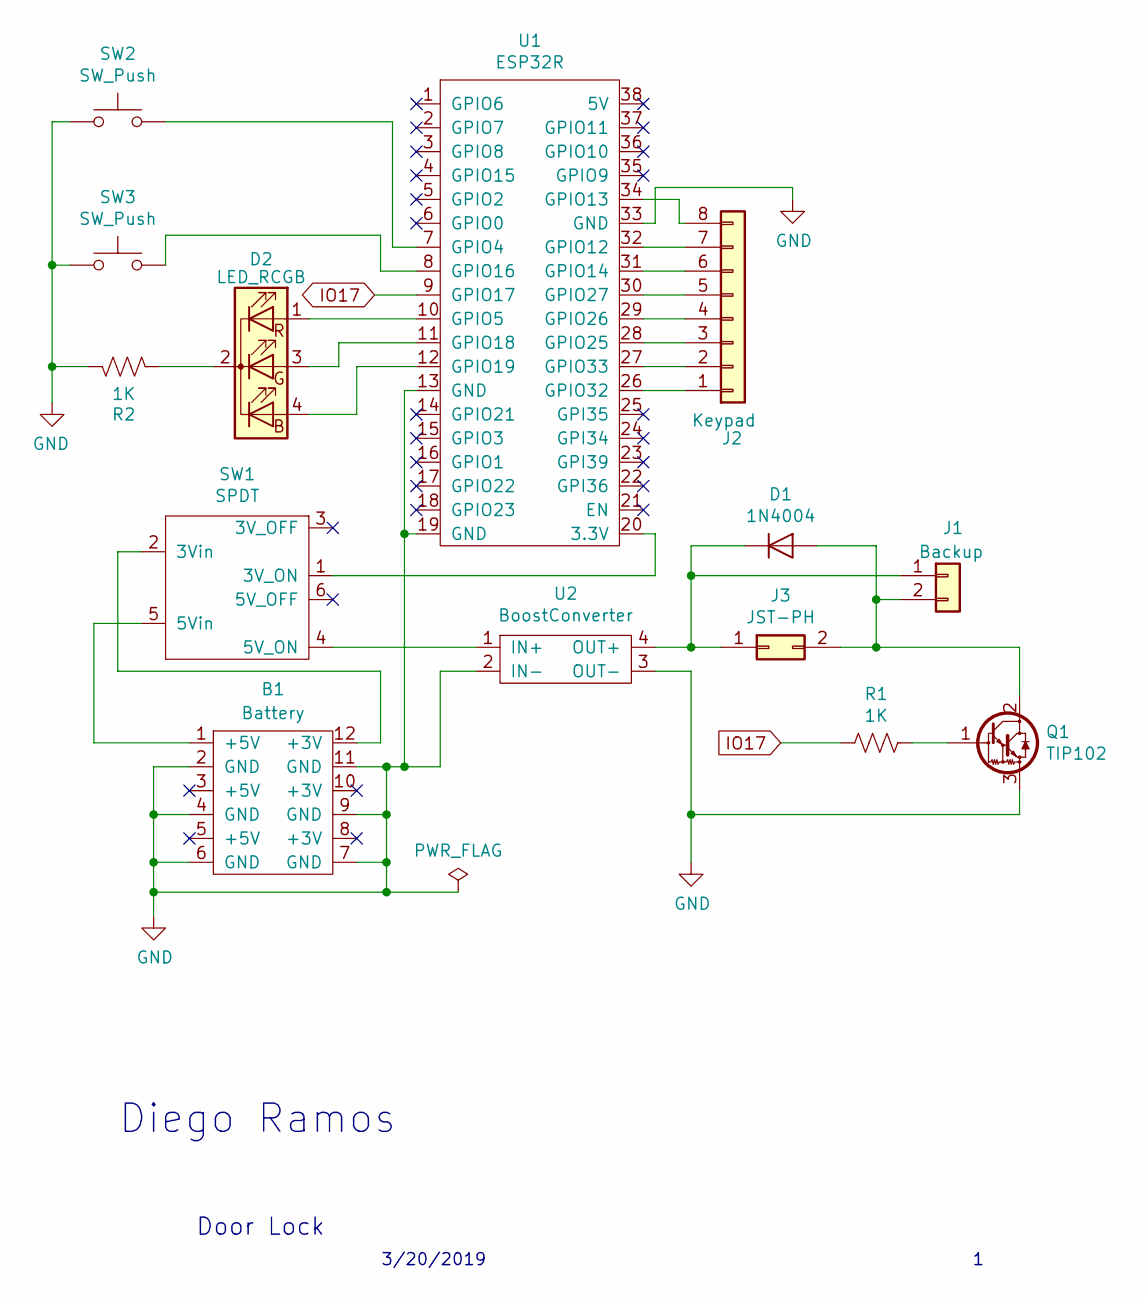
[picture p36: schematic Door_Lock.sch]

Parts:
B1: Battery; Battery_Supply
D1: 1N4004; D_DO-41_SOD81_P5.08mm_Vertical_AnodeUp
D2: LED_RCGB; LED_D5.0mm-4_RGB_Staggered_Pins
J1: Backup; PinHeader_1x02_P2.54mm_Vertical
J2: Keypad; PinSocket_1x08_P2.54mm_Vertical
J3: JST-PH
Q1: TIP102; TO-220-3_Vertical
R1: 1K; R_Axial_DIN0207_L6.3mm_D2.5mm_P7.62mm_Horizontal
R2: 1K; R_Axial_DIN0207_L6.3mm_D2.5mm_P2.54mm_Vertical
SW1: SPDT; PinSocket_2x03_P2.54mm_Vertical
SW2, SW3: SW_Push; SW_PUSH_6mm_H5mm
U1: ESP32R; ESP32_Diego
U2: BoostConverter

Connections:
GND: B1.2 (GND), B1.4 (GND), B1.6 (GND), B1.7 (GND), B1.9 (GND), B1.11 (GND), Q1.3, R2.2, SW2.1, SW3.1, U1.13 (GND), U1.19 (GND), U1.33 (GND), U2.2 (IN-), U2.3 (OUT-)
IO17: R1.2, U1.9 (GPIO17)
unnamed: B1.1 (+5V), SW1.5 (5Vin)
unnamed: B1.12 (+3V), SW1.2 (3Vin)
unnamed: D1.1 (K), J1.1, J3.1, U2.4 (OUT+)
unnamed: D1.2 (A), J1.2, J3.2, Q1.2
unnamed: D2.1 (RA), U1.10 (GPIO5)
unnamed: D2.2 (K), R2.1
unnamed: D2.3 (GA), U1.11 (GPIO18)
unnamed: D2.4 (BA), U1.12 (GPIO19)
unnamed: J2.1, U1.26 (GPIO32)
unnamed: J2.2, U1.27 (GPIO33)
unnamed: J2.3, U1.28 (GPIO25)
unnamed: J2.4, U1.29 (GPIO26)
unnamed: J2.5, U1.30 (GPIO27)
unnamed: J2.6, U1.31 (GPIO14)
unnamed: J2.7, U1.32 (GPIO12)
unnamed: J2.8, U1.34 (GPIO13)
unnamed: Q1.1, R1.1
unnamed: SW1.1 (3V_ON), U1.20 (3.3V)
unnamed: SW1.4 (5V_ON), U2.1 (IN+)
unnamed: SW2.2, U1.7 (GPIO4)
unnamed: SW3.2, U1.8 (GPIO16)

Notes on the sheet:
Door Lock
3/20/2019
Diego Ramos

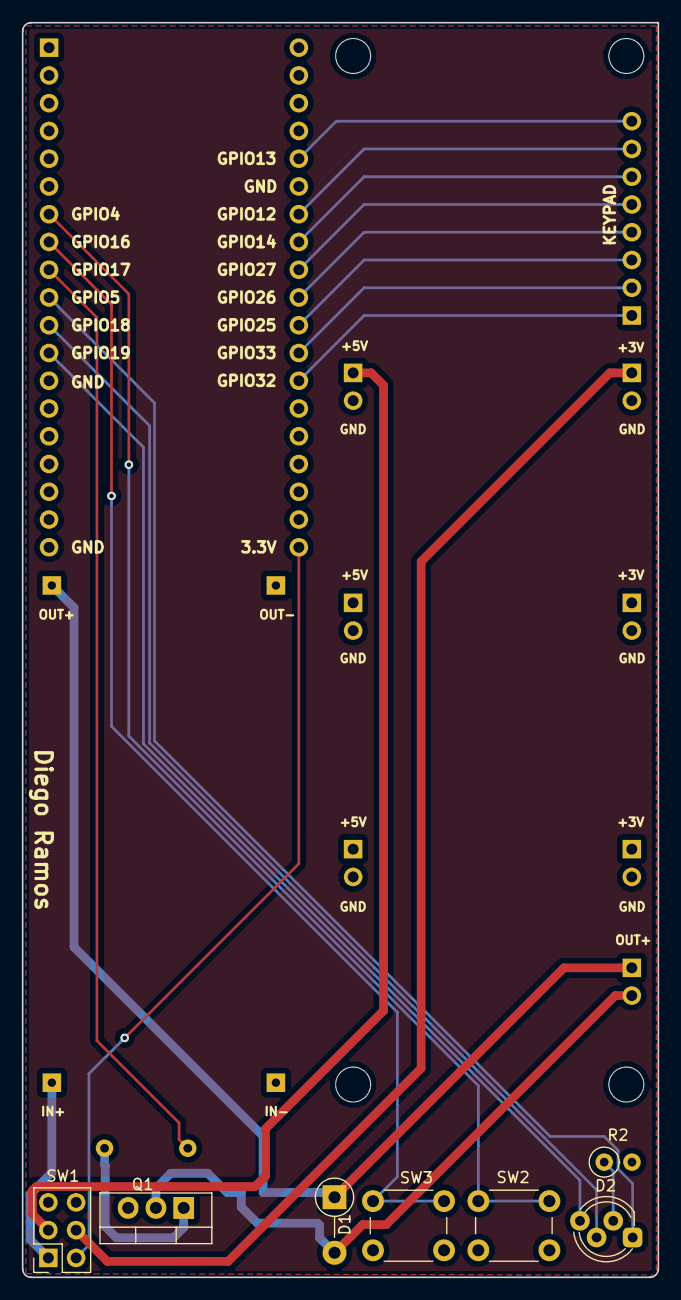
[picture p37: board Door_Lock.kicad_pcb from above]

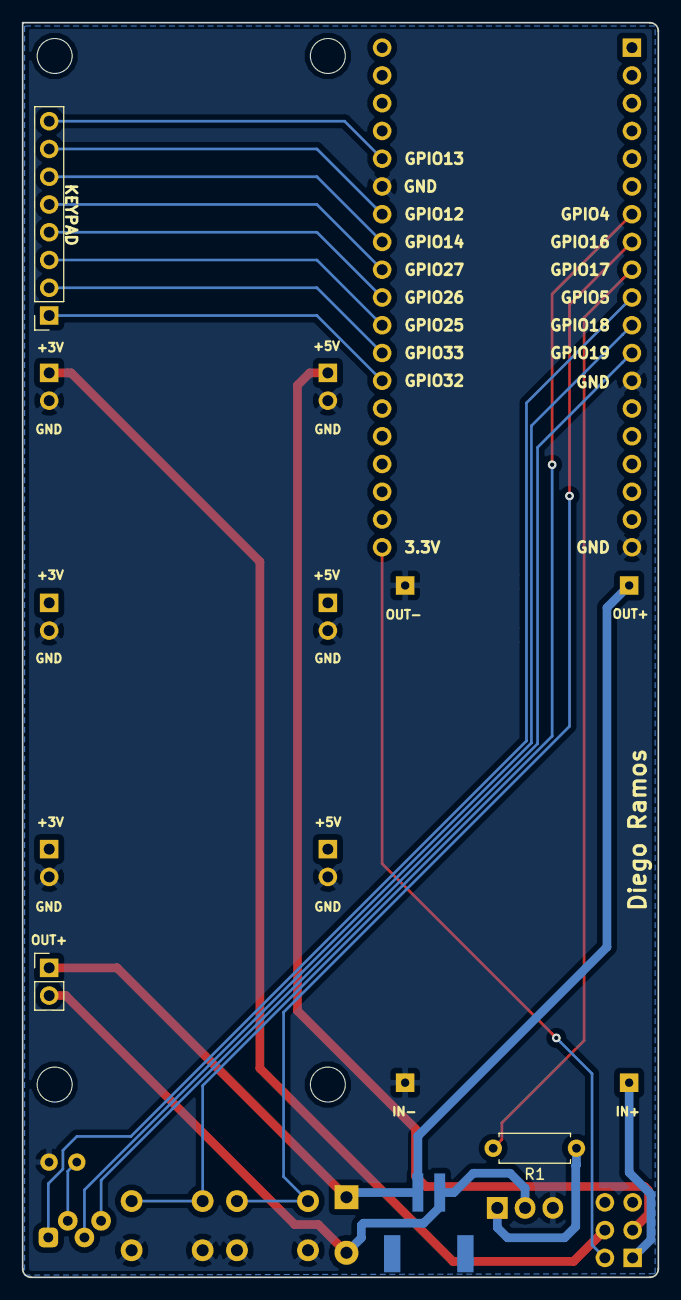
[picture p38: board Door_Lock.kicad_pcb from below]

Board: 2 copper layers, 58.2 x 114.8 mm, 16 parts (4 on the bottom side), 23 nets.

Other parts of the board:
HOLE1, HOLE3: MountingHole_3.2mm_M3

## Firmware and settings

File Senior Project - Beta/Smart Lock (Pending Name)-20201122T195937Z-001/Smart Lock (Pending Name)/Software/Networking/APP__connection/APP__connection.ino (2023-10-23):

#include <WiFi.h>

String  ClientRequest;
WiFiServer server(80);

WiFiClient client;

String myresultat;

String ReadIncomingRequest(){
while(client.available()) {
ClientRequest = (client.readStringUntil('\r'));
 if ((ClientRequest.indexOf("HTTP/1.1")>0)&&(ClientRequest.indexOf("/favicon.ico")<0)){
myresultat = ClientRequest;
}
}
return myresultat;
}

void setup()
{
ClientRequest = "";

Serial.begin(9600);

pinMode(5, OUTPUT);
  WiFi.disconnect();
  delay(3000);
  Serial.println("Attempting Connection to the Internet");
  WiFi.begin("NoMaste","01234567");
  while ((!(WiFi.status() == WL_CONNECTED))){
    delay(300);
    Serial.print(".");

  }
  Serial.println("Connection Successful! ");
  Serial.println("Place this IP into the search bar");
  Serial.println((WiFi.localIP()));
  server.begin();

}


void loop()
{

    client = server.available();
    if (!client) { return; }
    while(!client.available()){  delay(1); }
    ClientRequest = (ReadIncomingRequest());
    ClientRequest.remove(0, 5);
    ClientRequest.remove(ClientRequest.length()-9,9);
    if (ClientRequest == "OPEN") {
      digitalWrite(5,HIGH);

    }
    if (ClientRequest == "CLOSE") {
      digitalWrite(5,LOW);

    }
    client.println("HTTP/1.1 200 OK");
    client.println("Content-Type: text/html");
    client.println("");
    client.println("<!DOCTYPE HTML>");
    client.println("<html>");
    client.println("OK");
    client.println("</html>");
    client.stop();
    delay(1);
    client.flush();

}

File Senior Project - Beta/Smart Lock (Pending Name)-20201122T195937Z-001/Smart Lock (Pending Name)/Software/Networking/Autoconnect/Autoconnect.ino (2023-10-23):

#include <WiFi.h>          
#include <WebServer.h>     
#include <AutoConnect.h>   //Wifi Manager https://github.com/Hieromon/AutoConnect
#include <AutoConnectCredential.h>

#define ESP_SSID "ESP32" 
#define ESP_PASSWORD "ChipID12345" 

WiFiServer server(80);
WebServer Server;         
AutoConnect Portal(Server);
AutoConnectConfig Config;

void setup() {     
    Serial.begin(9600);
    pinMode (LED_BUILTIN, OUTPUT); //definning pairing LED 

void loop() {
   
}

void rootPage() {
  char content[] = "Smart Lock";
  Server.send(200, "text/plain", content);
}

//WiFI Pairing 
void Wifipairing(){   
  uint64_t chipid;
  chipid=ESP.getEfuseMac();
  ledblink(10,250,LED_BUILTIN);
  digitalWrite(LED_BUILTIN, HIGH);  
  Server.on("/", rootPage);
  Config.title = "Smart Lock";
  
  //Config.autoReconnect = true;
  Config.apid = ESP_SSID ; //+ (uint16_t)(chipid>>32)
  Config.psk = ESP_PASSWORD;
  Portal.config(Config);
  
  if (Portal.begin()) {
    Serial.println("WiFi connected: " + WiFi.localIP().toString()); 
  } 
